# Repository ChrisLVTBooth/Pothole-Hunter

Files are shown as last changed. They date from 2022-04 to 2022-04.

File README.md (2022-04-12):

# Pothole-Hunter
First steps towards a 'pothole hunter' as practice in designing, building and programming with sensor feedback

Pothole Hunter was developed for practice in designing, building and programming with sensor feedback. Developed in a 'Hardware' module of the MRAC course, the bot requires also python and other software programming to get the hardware to work as a roving bot capable of responding to specific objects detected by its sensors.
The initial concept was to build a small mobile robot to simulate detecting and filling potholes, which would require the ability to:
● recognize and detect potholes
● navigate to the closest pothole
● manoeuvre correctly to position an end effector directly over the pothole (done outside the system's field of vision)
● fill the pothole
● continue to the next pothole
In practice, the goals were scaled back while maintaining the core goal of learning to build and program a complete bot with sensor feedback. In practice the desired ability of recognizing and detecting potholes was simplified to recognizing and detecting 'blobs' within a colour range - in fact oranges as can be seen in the videos below! This simplification was mainly due to time constraints, brought about mainly by an unfortunate situation in which the timing of the development of the project came immediately after the release of the updated Raspberry Pi IV microcomputers but before any new software for the new 'camera stack' was generally available. This resulted in quite a lot of time being spent unsuccessfully trying to use the Raspberry Pi IV and the new official Raspberry Pi camera module together, which had to be abandoned due to the lack of software available at the time, and having to opt for an alternative object-recognition hardware/software solution, in a reduced timeframe. This is why the blog post contains some images with the Raspberry Pi camera module mounted in the bot, but the videos in fact use a mobile phone attached to the bot in order to use its camera instead.
Hardware Overview
The bot uses a simple rectangular aluminium frame (universally available 20mm x 20mm extrusion) below which are mounted two motorized wheels (DC motors with encoders, and motor drivers) and a castor wheel and above which is mounted the remaining hardware: an Arduino Uno R3 microprocessor (blue in image below) controls the motion system, a Raspberry Pi 4 microprocessor was intended to control the vision system, a Raspberry Pi V2 camera (both green in image below) but in the end a mobile phone was used as a camera (and off-board image processing was used instead of the Raspberry Pi 4). A 12V solenoid controlled the release of a liquid from a recipient to a tube which deposited it where the 'pothole' was. A distance sensor was positioned to detect when the liquid filled the 'pothole' to the required level. Screw couplings, 5V regulators, 3S Lipo batteries and some 3D printed parts completed the set up.
Hardware Bill Of Materials
If anyone wants to reproduce this bot completely or partially, the BOM lists the hardware elements, basic notes and a link to manufacturers information or suppliers.
Core Electronic Component Connections
The diagram fritzing.png, in the Misc images folder, shows the core electronic connections (it is high enough resolution to zoom in and identify all connections in detail), but the Raspberry Pi and its camera are not included because finally we did not use them.
However, if we had managed to use the Raspberry Pi 4 with the Camera Module 2, the Raspberry Pi would have received power from the H-Bridge 5V outputs (bottom right hand in image - the same as those from the H-Bridge to the Arduino Uno), the camera is always connected directly to the Raspberry Pi 4 with a cable attached to the camera at purchase (connection details here: https://projects.raspberrypi.org/en/projects/getting-started-with-picamera) and the connection between the Raspberry Pi and the Arduino Uno would have been by USB.
Steering
A key design element of the bot is the simplicity of the hardware layout for steering which allows relative simplicity in programming the bot's motion.
The bot has three wheels. One, the rear wheel, is a non-motorized castor wheel - it can rotate about a vertical axis to be able to point and move in any direction, but simply following the lead set by the other two wheels, which are identical and motorized. In this arrangement, if the left hand wheel is driven forward while the right hand wheel remains stationary, the bot rotates to the right. And conversely, if the right hand wheel is driven forward while the left hand wheel remains stationary, the bot rotates to the left. Of course if both powered wheels are driven together at the same speed, the bot moves straight forward. These three options are shown in the image Pothole hunter - Steering I.png.
Simultaneously, our requirements in terms of navigating directly towards a detected object in the field of vision are very similar: assuming the vision system is looking straight forward in front of the bot, if an object is detected in the right hand part of the image, then the bot needs to be rotated to the right to be pointing straight at it. Conversely, if an object is detected in the left hand part of the image, then the bot needs to be rotated to the left to be pointing straight at it. Of course when an object is detected at the centre of the image the bot is already pointing straight at it and so needs to be driven stright forward to reach it. These three options are shown in Pothole Hunter - Steering II.png. 
Pseudocode
The logic of these simple movements is at the core of the 'pseudocode' which lets us move from what the vision system detects (an object in the left, centre, or right of a series of frames) to giving appropriate instructions to the wheels to achieve the desired goal - steering the bot until the detected object is at the bottom of the centre of the field of vision. When this is achieved, which is called 'Oriented' in the pseudocode image below, a fourth movement option (additional to Turn left, Go straight and Turn right) is programmed which is called 'Move to hole'.

'Move to hole' is a movement straight forward the required distance to position the liquid-dispensing hardware of the bot, consisting of a small recipient a solenoid and a tube, directly over the point where the detected object left the field of vision.
The image 'Pothole Hunter Pseudocode 02.png' shows this pseudocode graphically.

In the pseudocode shown graphically in 'Pothole Hunter Pseudocode 02.png' shows the entire process. Unlike previous pseudocode described, which focuses on linking the vision system to the steering, this pseudocode includes the process of filling the pothole. Our bot did have a functioning 'pothole filling system' - the solenoid was functional and the python coding included to begin to release liquid after the bot was positioned over the 'pothole' and to stop releasing liquid when a sensor detected a fill-level had been reached - but its use does not appear in any videos since our detection was restricted to orange blobs and not potholes. 

Actual Code

There is python code - pothole hunter.py - written to be run on the Raspberry Pi but finally run on a laptop because of the camera stack problems with the new Raspberry Pi 4. It is in the Code folder.
The code for the Arduino Uno is also there - Arduino.ino

There are several videos of the 'Pothole Hunter' in action in the Videos folder.

Pothole Hunter is a project of IAAC, Institute for Advanced Architecture of Catalonia, developed at the Master of Robotics and Advanced Construction in 2021-2022 by:
Students: Huanyu Li, Libish Murugesan, Christopher Booth and Tomás Quijano
Faculty: Oscar Gonzalez, and Assistant Faculty: Daniil Koshelyuk

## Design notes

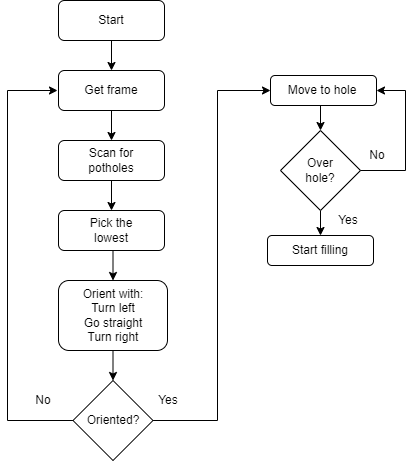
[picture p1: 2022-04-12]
Misc images/Pothole Hunter Pseudocode 02.png

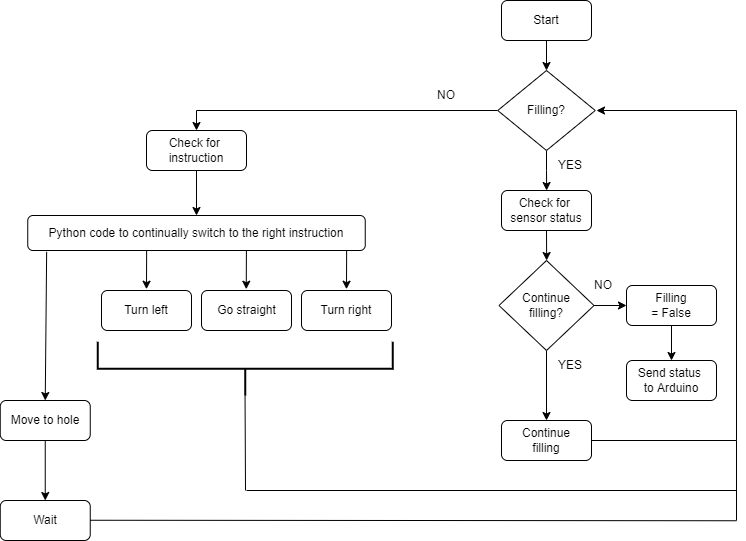
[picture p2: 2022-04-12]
Misc images/Pothole Hunter Pseudocode 01.png

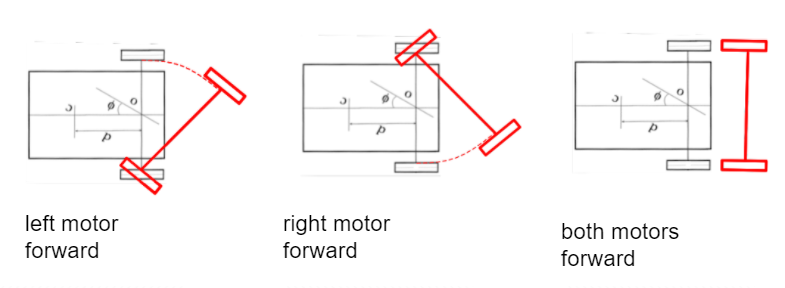
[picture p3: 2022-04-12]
Misc images/Pothole hunter - Steering I.png

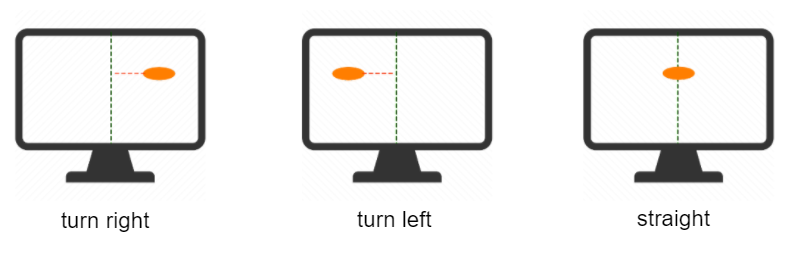
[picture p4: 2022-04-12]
Misc images/Pothole Hunter - Steering II.png

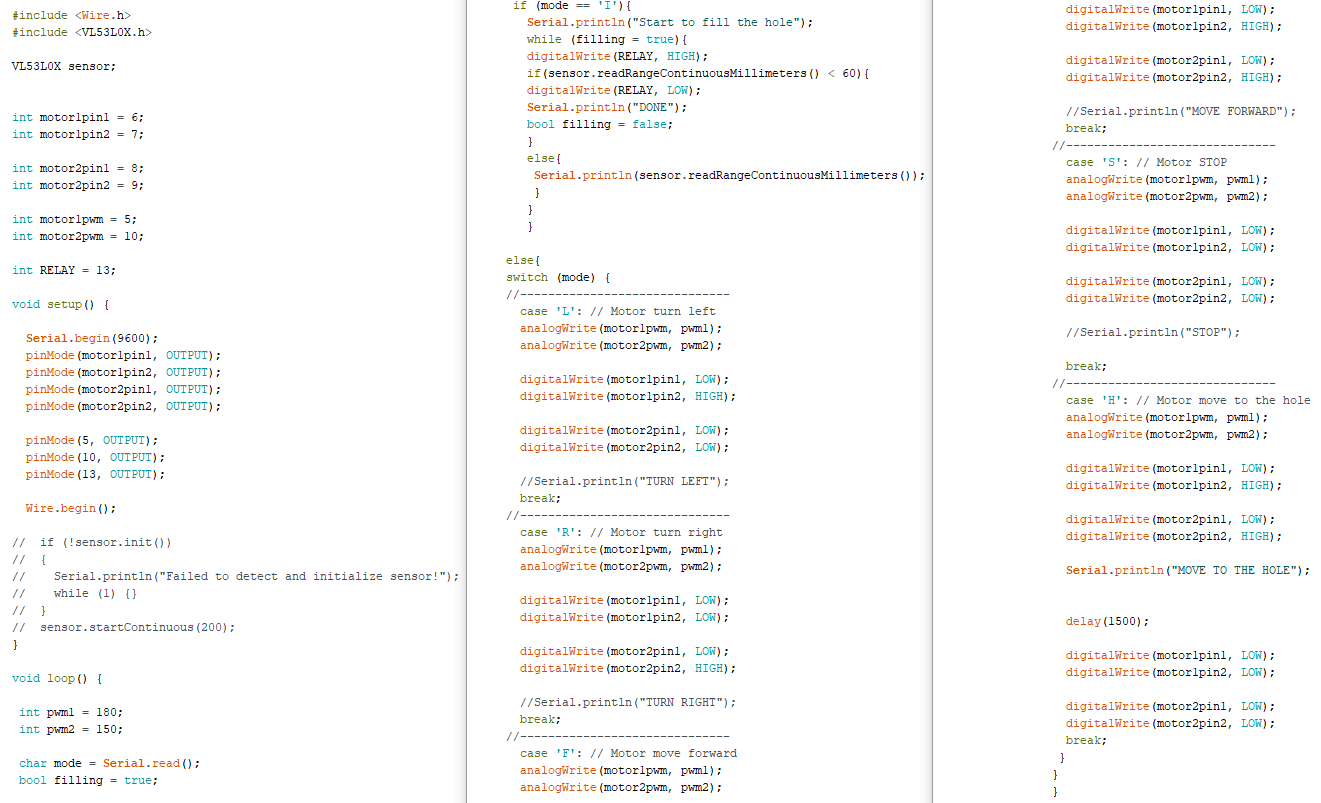
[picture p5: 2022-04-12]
Misc images/Arduino Code Complete.png

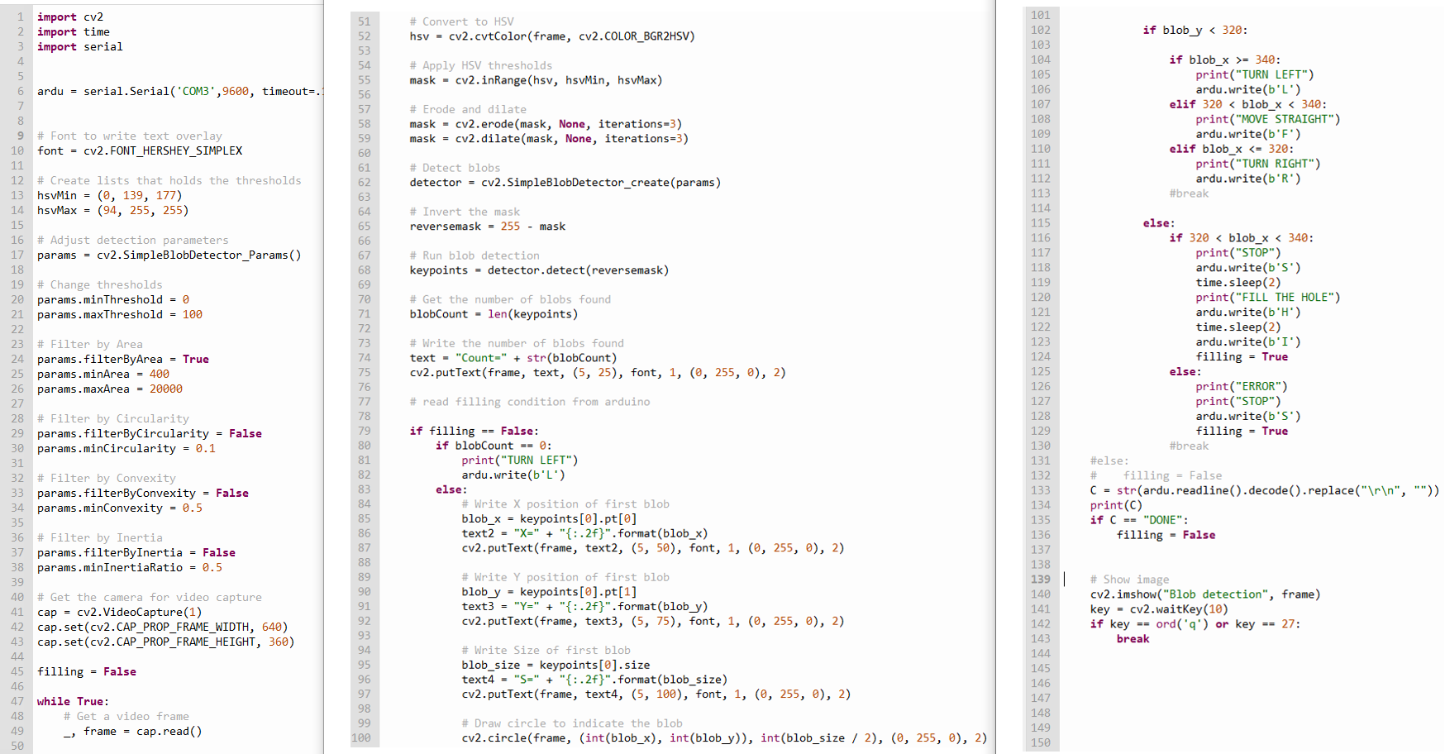
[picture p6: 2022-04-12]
Misc images/Python Code Complete.png

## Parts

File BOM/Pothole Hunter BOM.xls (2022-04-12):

HARDWARE | COMMENTS/NOTES | SOURCE
Microprocessors
Raspberry Pi 4 (2GB) | OS = Raspberry Pi 64 Bit | https://www.raspberrypi.com/products/raspberry-pi-4-model-b/
Arduino Uno | Arduino IDE 1.8.19 | https://store.arduino.cc/products/arduino-uno-rev3
Intended Vision Solution
Raspberry Pi Camera Module 2 NoIR (8MP) | Original Plan: Obtain camera data and pass to Opencv installed on the Raspberry Pi. Process on-board and pass results to Python code for navigation, also on the Raspberry Pi. Pass the resulting navigation commands by cable to the Arduino. The Arduino code processes the navigation instructions through to motorizing the driven wheels. | https://www.raspberrypi.com/products/pi-noir-camera-v2/
Fallback Vision Solution
Mobile Phone Camera | Fallback Plan: Obtain camera data by webcam on mobile phone and pass to Opencv installed on laptop. Process on laptop and pass results to Python code for navigation, also on the laptop. Pass the resulting navigation commands by cable to the Arduino. The Arduino code processes the navigation instructions through to motorizing the driven wheels.
Drive System
Lipo Battery 1300mAh 3S 25C, 11.1V – XT60 | https://en.wikipedia.org/wiki/Lithium_polymer_battery | https://tienda.bricogeek.com/baterias-lipo/1402-bateria-lipo-1300mah-3s-25c-11-1v.html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
12V DC Motor with Encoder(100rpm) (x2) | Be aware that with 12V DC motors and the microprocessors requiring a 5V power supply, the wiring has to be routed through a convertor – see details in the 'Miscellaneous' section | https://www.amazon.es/turbina-schneckengetriebemotor-Encoder-Incluso-Bloqueo/dp/B07J2CFGZG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
L298N Motor driver(x2) |  | https://www.amazon.es/TECNOIOT-Driver-Stepper-Controller-Module/dp/B07YXFQ8CZ?ref_=ast_sto_dp
Wheels 80mm diameter (x2) |  | https://tienda.bricogeek.com/robotica/303-pareja-de-ruedas-80x10mm-blanco.html
Pothole 'Infill Detection' & Filling
VL53L0X Distance Sensor |  | https://www.amazon.es/ICQUANZX-VL53L0X-Detecci%C3%B3n-medici%C3%B3n-Distancia/dp/B07VJ87PZC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
DC 12/24V Electric Solenoid Valve | In case of reproducing this 'liquid deposition' system, we recommend a more expensive solenoid diaphragm valve: this cheap one did not close 'hermetically' (it dripped easily) | https://www.amazon.es/OSISTER7-solenoide-electromagn%C3%A9tica-normalmente-conntecci%C3%B3n/dp/B08M3CYKYJ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
Miscellaneous
JZK 24V/12V to 5V 5A DC-DC Step Down Power Supply Converter | The 11.1V Battery connected directly to the 12V DC motors but the power supply for the Raspberry Pi and Arduino require around 5V, achieved with this converter | https://www.jzk-jzk.com/products/24v-12v-to-5v-5a-power-buck-module-dc-dc-step-down-power-supply-converter-with-led
5V Relay Module for Arduino |  | https://www.amazon.com/Tolako-Arduino-Indicator-Channel-Official/dp/B00VRUAHLE
Generic Castor Wheel | e.g. as typically found on office chairs | Any castor wheel of appropriate size to level the frame to the height of the motorized wheels
Screw couplings (for connecting the wheels to the motors) |  | https://tienda.bricogeek.com/accesorios-motores/826-soporte-de-eje-6mm-m3.html
Miscellaneous 3D Printed Parts | Bracket for DC Motor holders

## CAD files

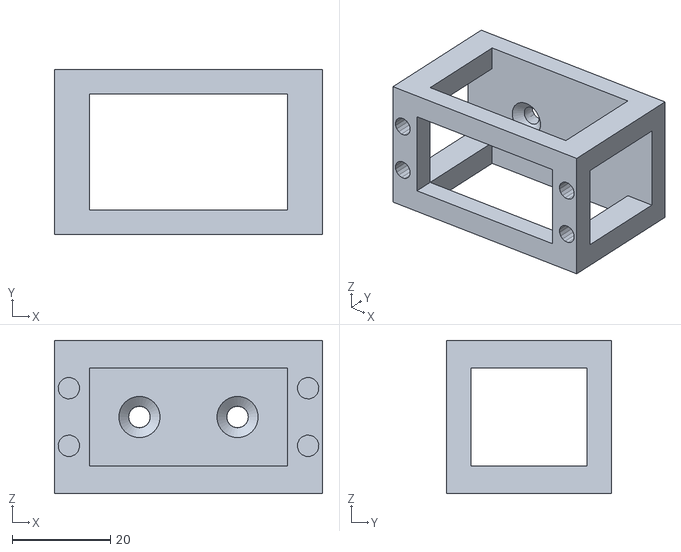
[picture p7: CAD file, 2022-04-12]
3D Prints/PiC_Servo.stl
54.7 x 33.6 x 31.2

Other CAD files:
3D Prints/PiC_Servo.3dm

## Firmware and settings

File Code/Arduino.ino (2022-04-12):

#include <Wire.h>
#include <VL53L0X.h>

VL53L0X sensor;


int motor1pin1 = 6;
int motor1pin2 = 7;

int motor2pin1 = 8;
int motor2pin2 = 9;

int motor1pwm = 5;
int motor2pwm = 10;

int RELAY = 13;

void setup() {
  
  Serial.begin(9600);
  pinMode(motor1pin1, OUTPUT);
  pinMode(motor1pin2, OUTPUT);
  pinMode(motor2pin1, OUTPUT);
  pinMode(motor2pin2, OUTPUT);

  pinMode(5, OUTPUT); 
  pinMode(10, OUTPUT);
  pinMode(13, OUTPUT);

  Wire.begin();

//  if (!sensor.init())
//  {
//    Serial.println("Failed to detect and initialize sensor!");
//    while (1) {}
//  }
//  sensor.startContinuous(200);
}

   

void loop() {

 int pwm1 = 180;
 int pwm2 = 150;
 
 char mode = Serial.read(); 
 bool filling = true;

 if (mode == 'I'){
   Serial.println("Start to fill the hole");
   while (filling = true){
   digitalWrite(RELAY, HIGH);
   if(sensor.readRangeContinuousMillimeters() < 60){
   digitalWrite(RELAY, LOW);
   Serial.println("DONE");
   bool filling = false;
   }
   else{
    Serial.println(sensor.readRangeContinuousMillimeters());
    } 
   }
   }

else{
switch (mode) {
//------------------------------
  case 'L': // Motor turn left
  analogWrite(motor1pwm, pwm1);
  analogWrite(motor2pwm, pwm2);

  digitalWrite(motor1pin1, LOW);
  digitalWrite(motor1pin2, HIGH);

  digitalWrite(motor2pin1, LOW);
  digitalWrite(motor2pin2, LOW);

  //Serial.println("TURN LEFT"); 
  break;
//------------------------------
  case 'R': // Motor turn right
  analogWrite(motor1pwm, pwm1);
  analogWrite(motor2pwm, pwm2);

  digitalWrite(motor1pin1, LOW);
  digitalWrite(motor1pin2, LOW);

  digitalWrite(motor2pin1, LOW);
  digitalWrite(motor2pin2, HIGH);

  //Serial.println("TURN RIGHT"); 
  break;
//------------------------------
  case 'F': // Motor move forward
  analogWrite(motor1pwm, pwm1);
  analogWrite(motor2pwm, pwm2);

  digitalWrite(motor1pin1, LOW);
  digitalWrite(motor1pin2, HIGH);

  digitalWrite(motor2pin1, LOW);
  digitalWrite(motor2pin2, HIGH);

  //Serial.println("MOVE FORWARD"); 
  break;
//------------------------------
  case 'S': // Motor STOP
  analogWrite(motor1pwm, pwm1);
  analogWrite(motor2pwm, pwm2);

  digitalWrite(motor1pin1, LOW);
  digitalWrite(motor1pin2, LOW);

  digitalWrite(motor2pin1, LOW);
  digitalWrite(motor2pin2, LOW);

  //Serial.println("STOP"); 

  break;
//------------------------------
  case 'H': // Motor move to the hole
  analogWrite(motor1pwm, pwm1);
  analogWrite(motor2pwm, pwm2);

  digitalWrite(motor1pin1, LOW);
  digitalWrite(motor1pin2, HIGH);

  digitalWrite(motor2pin1, LOW);
  digitalWrite(motor2pin2, HIGH);

  Serial.println("MOVE TO THE HOLE"); 


  delay(1500);

  digitalWrite(motor1pin1, LOW);
  digitalWrite(motor1pin2, LOW);

  digitalWrite(motor2pin1, LOW);
  digitalWrite(motor2pin2, LOW);
  break;
 } 
}
}

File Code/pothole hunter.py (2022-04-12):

import cv2
import time
import serial


ardu = serial.Serial('COM3',9600, timeout=.1)






# Font to write text overlay
font = cv2.FONT_HERSHEY_SIMPLEX

# Create lists that holds the thresholds
hsvMin = (0, 139, 177)
hsvMax = (94, 255, 255)

# Adjust detection parameters
params = cv2.SimpleBlobDetector_Params()

# Change thresholds
params.minThreshold = 0
params.maxThreshold = 100

# Filter by Area
params.filterByArea = True
params.minArea = 400
params.maxArea = 20000

# Filter by Circularity
params.filterByCircularity = False
params.minCircularity = 0.1

# Filter by Convexity
params.filterByConvexity = False
params.minConvexity = 0.5

# Filter by Inertia
params.filterByInertia = False
params.minInertiaRatio = 0.5

# Get the camera for video capture
cap = cv2.VideoCapture(1)
cap.set(cv2.CAP_PROP_FRAME_WIDTH, 640)
cap.set(cv2.CAP_PROP_FRAME_HEIGHT, 360)

filling = False

while True:
    # Get a video frame
    _, frame = cap.read()

    # Convert to HSV
    hsv = cv2.cvtColor(frame, cv2.COLOR_BGR2HSV)

    # Apply HSV thresholds
    mask = cv2.inRange(hsv, hsvMin, hsvMax)

    # Erode and dilate
    mask = cv2.erode(mask, None, iterations=3)
    mask = cv2.dilate(mask, None, iterations=3)

    # Detect blobs
    detector = cv2.SimpleBlobDetector_create(params)

    # Invert the mask
    reversemask = 255 - mask

    # Run blob detection
    keypoints = detector.detect(reversemask)

    # Get the number of blobs found
    blobCount = len(keypoints)

    # Write the number of blobs found
    text = "Count=" + str(blobCount)
    cv2.putText(frame, text, (5, 25), font, 1, (0, 255, 0), 2)

    # read filling condition from arduino

    if filling == False:
        if blobCount == 0:
            print("TURN LEFT")
            ardu.write(b'L')
        else:
            # Write X position of first blob
            blob_x = keypoints[0].pt[0]
            text2 = "X=" + "{:.2f}".format(blob_x)
            cv2.putText(frame, text2, (5, 50), font, 1, (0, 255, 0), 2)

            # Write Y position of first blob
            blob_y = keypoints[0].pt[1]
            text3 = "Y=" + "{:.2f}".format(blob_y)
            cv2.putText(frame, text3, (5, 75), font, 1, (0, 255, 0), 2)

            # Write Size of first blob
            blob_size = keypoints[0].size
            text4 = "S=" + "{:.2f}".format(blob_size)
            cv2.putText(frame, text4, (5, 100), font, 1, (0, 255, 0), 2)

            # Draw circle to indicate the blob
            cv2.circle(frame, (int(blob_x), int(blob_y)), int(blob_size / 2), (0, 255, 0), 2)

            if blob_y < 320:

                if blob_x >= 340:
                    print("TURN LEFT")
                    ardu.write(b'L')
                elif 320 < blob_x < 340:
                    print("MOVE STRAIGHT")
                    ardu.write(b'F')
                elif blob_x <= 320:
                    print("TURN RIGHT")
                    ardu.write(b'R')
                #break

            else:
                if 320 < blob_x < 340:
                    print("STOP")
                    ardu.write(b'S')
                    time.sleep(2)
                    print("FILL THE HOLE")
                    ardu.write(b'H')
                    time.sleep(2)
                    ardu.write(b'I')
                    filling = True
                else:
                    print("ERROR")
                    print("STOP")
                    ardu.write(b'S')
                    filling = True
                #break
    #else:
    #    filling = False
    C = str(ardu.readline().decode().replace("\r\n", ""))
    print(C)
    if C == "DONE":
        filling = False


    # Show image
    cv2.imshow("Blob detection", frame)
    key = cv2.waitKey(10)
    if key == ord('q') or key == 27:
        break
